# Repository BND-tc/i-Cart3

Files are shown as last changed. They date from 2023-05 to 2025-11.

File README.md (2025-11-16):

# i-Cart3

オープンソース移動ロボットプラットフォームi-Cart3 の制作に必要な情報のリポジトリ

## パーツリスト (Parts list)
60W/100W/200Wモーター版の組立に必要な部品構成表です

## 3Dモデルデータ (3D Model Data)
Parasolid形式とSTEP形式のモデルデータです

## 構成 (Configuraion)
システムおよび回路の構成の資料です

iCart3_Configuration.pdfを参考に配線をしてください

## ソフトウェア (Software)
i-Cart3用のソフトウェアおよび設定ファイルです

### yp-spur(BLVR対応)
> https://github.com/BND-tc/yp-spur

上記ビルドの際にはlibmodbusが必要となります

BLVRにはあらかじめ左右モータードライバにmxex設定ファイルを適用してください

### yp-spur単体実行例
> /usr/local/bin/ypspur-coordinator -d PORT_PATH --blvr -p PARAM_PATH

> /usr/local/bin/ypspur-coordinator -d /dev/ttyUSB0 --blvr -p /home/pi/iCart3_200W.param

### ros実行例
> rosrun ypspur_ros ypspur_ros _ypspur_bin:=/usr/local/bin/ypspur-coordinator _port:=[PORT_PATH]--blvr _param_file:=[PARAM_PATH] _compatible:=1

> rosrun ypspur_ros ypspur_ros _ypspur_bin:=/usr/local/bin/ypspur-coordinator _port:=/dev/ttyUSB0--blvr _param_file:=/home/pi/iCart3_200W.param _compatible:=1

<strong> --blvrオプションの記載をデバイスポートの直後にスペース無しで記載してください。</strong>

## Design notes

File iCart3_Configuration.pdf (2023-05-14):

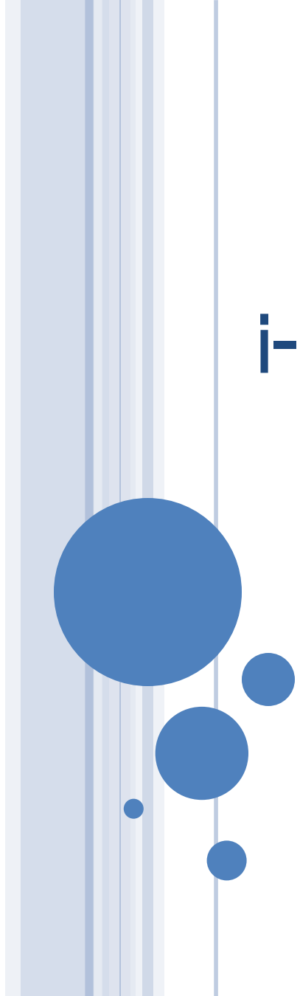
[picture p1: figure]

# i-Cart3

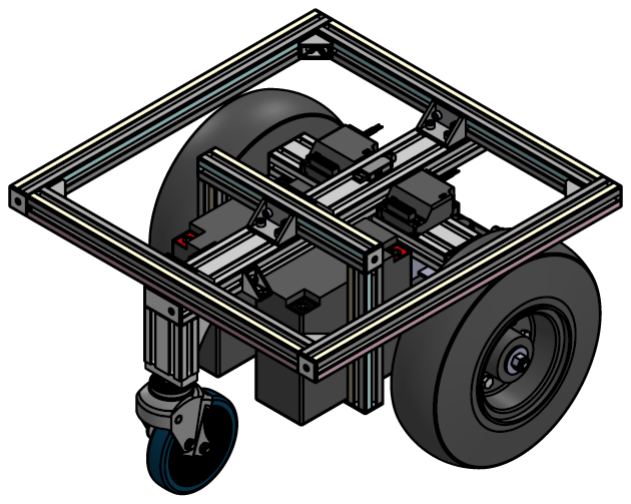
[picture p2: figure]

## https://github.com/BND-tc/i-Cart3

# 1 System Configuration

PC

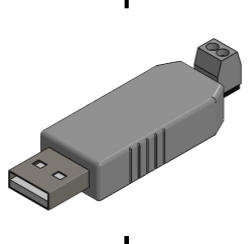
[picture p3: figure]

## USB-RS485 Convertor

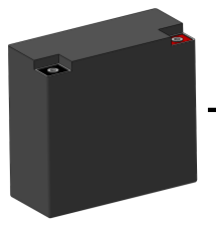
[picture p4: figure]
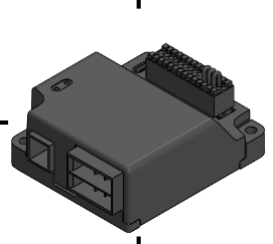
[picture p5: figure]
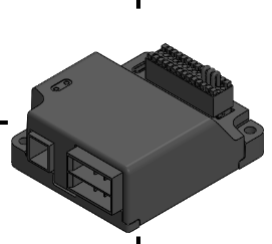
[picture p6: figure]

## BLVR

BLDC motor driver

## BLDC Motor

## Battery

# 2 Circuit Configuration

PC

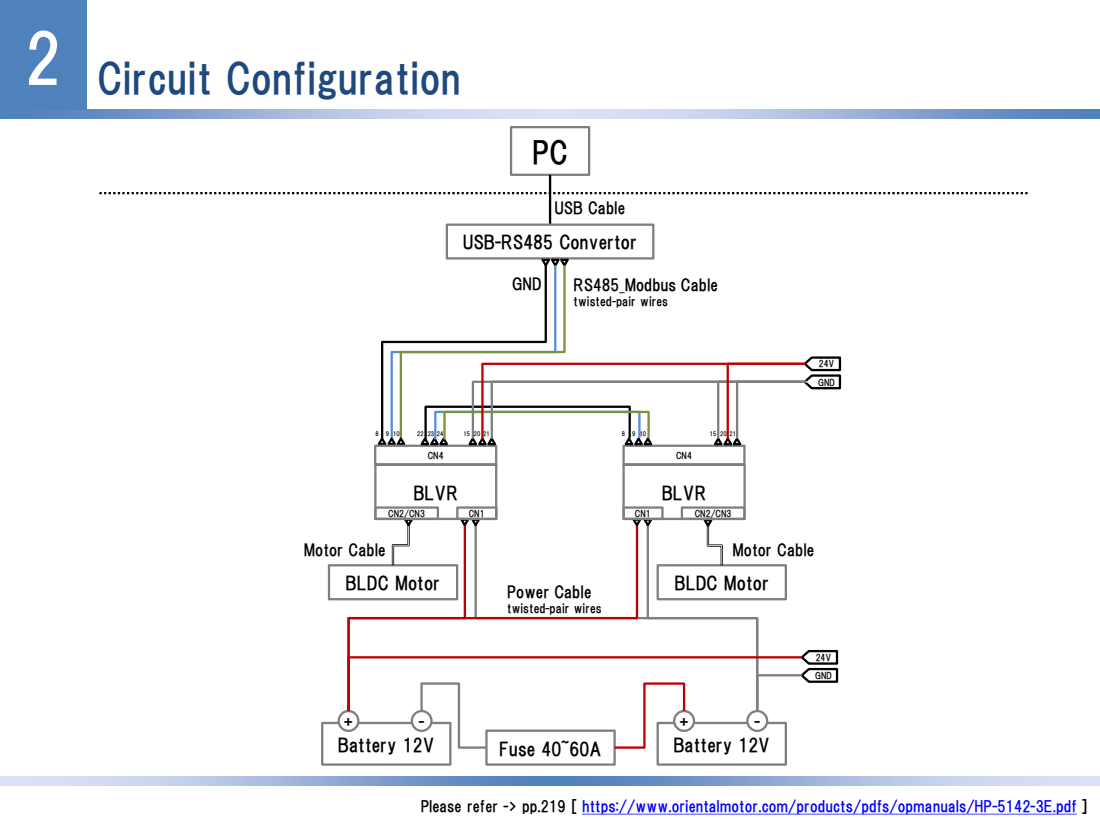
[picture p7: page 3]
USB-RS485 Convertor; BLVR; BLDC Motor; Fuse 40~60A; USB Cable; Motor; Cable; Motor Cable; Battery 12V; GND

RS485_Modbus Cable
twisted-pair wires

Power Cable

Please refer -> pp.219 [ https://www.orientalmotor.com/products/pdfs/opmanuals/HP-5142-3E.pdf ]

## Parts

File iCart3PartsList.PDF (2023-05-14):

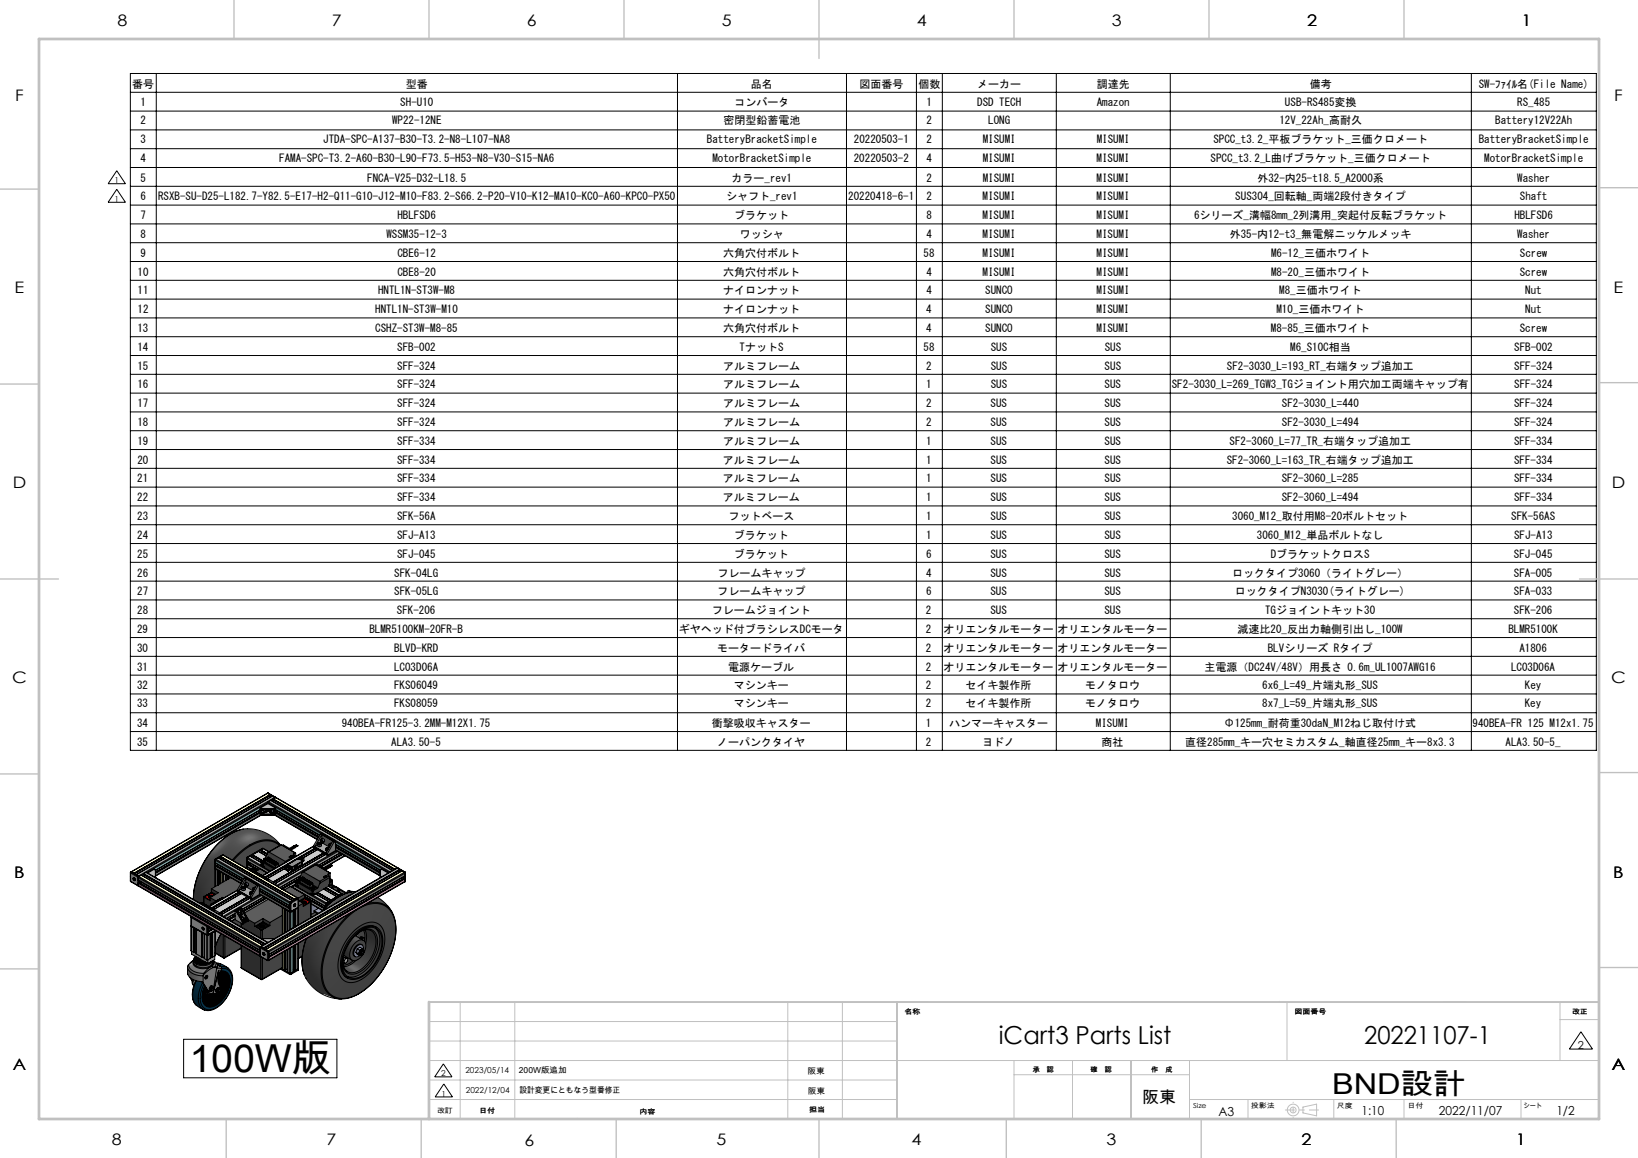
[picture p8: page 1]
2022/12/04 設計変更にともなう型番修正; 2023/05/14 200W版追加; iCart3 Parts List; BND設計; 1:10 投影法 改訂

番号 | 型番 | 品名 | 図面番号 | 個数 | メーカー | 調達先 | 備考 | SW-ﾌｧｲﾙ名(File Name)
1 | SH-U10 | コンバータ | | 1 | DSD TECH | Amazon | USB-RS485変換 | RS_485
2 | WP22-12NE | 密閉型鉛蓄電池 | | 2 | LONG | | 12V_22Ah_高耐久 | Battery12V22Ah
3 | JTDA-SPC-A137-B30-T3.2-N8-L107-NA8 | BatteryBracketSimple | 20220503-1 | 2 | MISUMI | MISUMI | SPCC_t3.2_平板ブラケット_三価クロメート | BatteryBracketSimple
4 | FAMA-SPC-T3.2-A60-B30-L90-F73.5-H53-N8-V30-S15-NA6 | MotorBracketSimple | 20220503-2 | 4 | MISUMI | MISUMI | SPCC_t3.2_L曲げブラケット_三価クロメート | MotorBracketSimple
5 | FNCA-V25-D32-L18.5 | カラー_rev1 | | 2 | MISUMI | MISUMI | 外32-内25-t18.5_A2000系 | Washer
6 | RSXB-SU-D25-L182.7-Y82.5-E17-H2-Q11-G10-J12-M10-F83.2-S66.2-P20-V10-K12-MA10-KC0-A60-KPC0-PX50 | シャフト_rev1 | 20220418-6-1 | 2 | MISUMI | MISUMI | SUS304_回転軸_両端2段付きタイプ | Shaft
7 | HBLFSD6 | ブラケット | | 8 | MISUMI | MISUMI | 6シリーズ_溝幅8mm_2列溝用_突起付反転ブラケット | HBLFSD6
8 | WSSM35-12-3 | ワッシャ | | 4 | MISUMI | MISUMI | 外35-内12-t3_無電解ニッケルメッキ | Washer
9 | CBE6-12 | 六角穴付ボルト | | 58 | MISUMI | MISUMI | M6-12_三価ホワイト | Screw
10 | CBE8-20 | 六角穴付ボルト | | 4 | MISUMI | MISUMI | M8-20_三価ホワイト | Screw
11 | HNTL1N-ST3W-M8 | ナイロンナット | | 4 | SUNCO | MISUMI | M8_三価ホワイト | Nut
12 | HNTL1N-ST3W-M10 | ナイロンナット | | 4 | SUNCO | MISUMI | M10_三価ホワイト | Nut
13 | CSHZ-ST3W-M8-85 | 六角穴付ボルト | | 4 | SUNCO | MISUMI | M8-85_三価ホワイト | Screw
14 | SFB-002 | TナットS | | 58 | SUS | SUS | M6_S10C相当 | SFB-002
15 | SFF-324 | アルミフレーム | | 2 | SUS | SUS | SF2-3030_L=193_RT_右端タップ追加工 | SFF-324
16 | SFF-324 | アルミフレーム | | 1 | SUS | SUS | SF2-3030_L=269_TGW3_TGジョイント用穴加工両端キャップ有 | SFF-324
17 | SFF-324 | アルミフレーム | | 2 | SUS | SUS | SF2-3030_L=440 | SFF-324
18 | SFF-324 | アルミフレーム | | 2 | SUS | SUS | SF2-3030_L=494 | SFF-324
19 | SFF-334 | アルミフレーム | | 1 | SUS | SUS | SF2-3060_L=77_TR_右端タップ追加工 | SFF-334
20 | SFF-334 | アルミフレーム | | 1 | SUS | SUS | SF2-3060_L=163_TR_右端タップ追加工 | SFF-334
21 | SFF-334 | アルミフレーム | | 1 | SUS | SUS | SF2-3060_L=285 | SFF-334
22 | SFF-334 | アルミフレーム | | 1 | SUS | SUS | SF2-3060_L=494 | SFF-334
23 | SFK-56A | フットベース | | 1 | SUS | SUS | 3060_M12_取付用M8-20ボルトセット | SFK-56AS
24 | SFJ-A13 | ブラケット | | 1 | SUS | SUS | 3060_M12_単品ボルトなし | SFJ-A13
25 | SFJ-045 | ブラケット | | 6 | SUS | SUS | DブラケットクロスS | SFJ-045
26 | SFK-04LG | フレームキャップ | | 4 | SUS | SUS | ロックタイプ3060（ライトグレー） | SFA-005
27 | SFK-05LG | フレームキャップ | | 6 | SUS | SUS | ロックタイプN3030(ライトグレー) | SFA-033
28 | SFK-206 | フレームジョイント | | 2 | SUS | SUS | TGジョイントキット30 | SFK-206
29 | BLMR5100KM-20FR-B | ギヤヘッド付ブラシレスDCモータ | | 2 | オリエンタルモーター | オリエンタルモーター | 減速比20_反出力軸側引出し_100W | BLMR5100K
30 | BLVD-KRD | モータードライバ | | 2 | オリエンタルモーター | オリエンタルモーター | BLVシリーズ Rタイプ | A1806
31 | LC03D06A | 電源ケーブル | | 2 | オリエンタルモーター | オリエンタルモーター | 主電源（DC24V/48V）用長さ 0.6m_UL1007AWG16 | LC03D06A
32 | FKS06049 | マシンキー | | 2 | セイキ製作所 | モノタロウ | 6x6_L=49_片端丸形_SUS | Key
33 | FKS08059 | マシンキー | | 2 | セイキ製作所 | モノタロウ | 8x7_L=59_片端丸形_SUS | Key
34 | 940BEA-FR125-3.2MM-M12X1.75 | 衝撃吸収キャスター | | 1 | ハンマーキャスター | MISUMI | Φ125mm_耐荷重30daN_M12ねじ取付け式 | 940BEA-FR 125 M12x1.75
35 | ALA3.50-5 | ノーパンクタイヤ | | 2 | ヨドノ | 商社 | 直径285mm_キー穴セミカスタム_軸直径25mm_キー8x3.3 | ALA3.50-5_

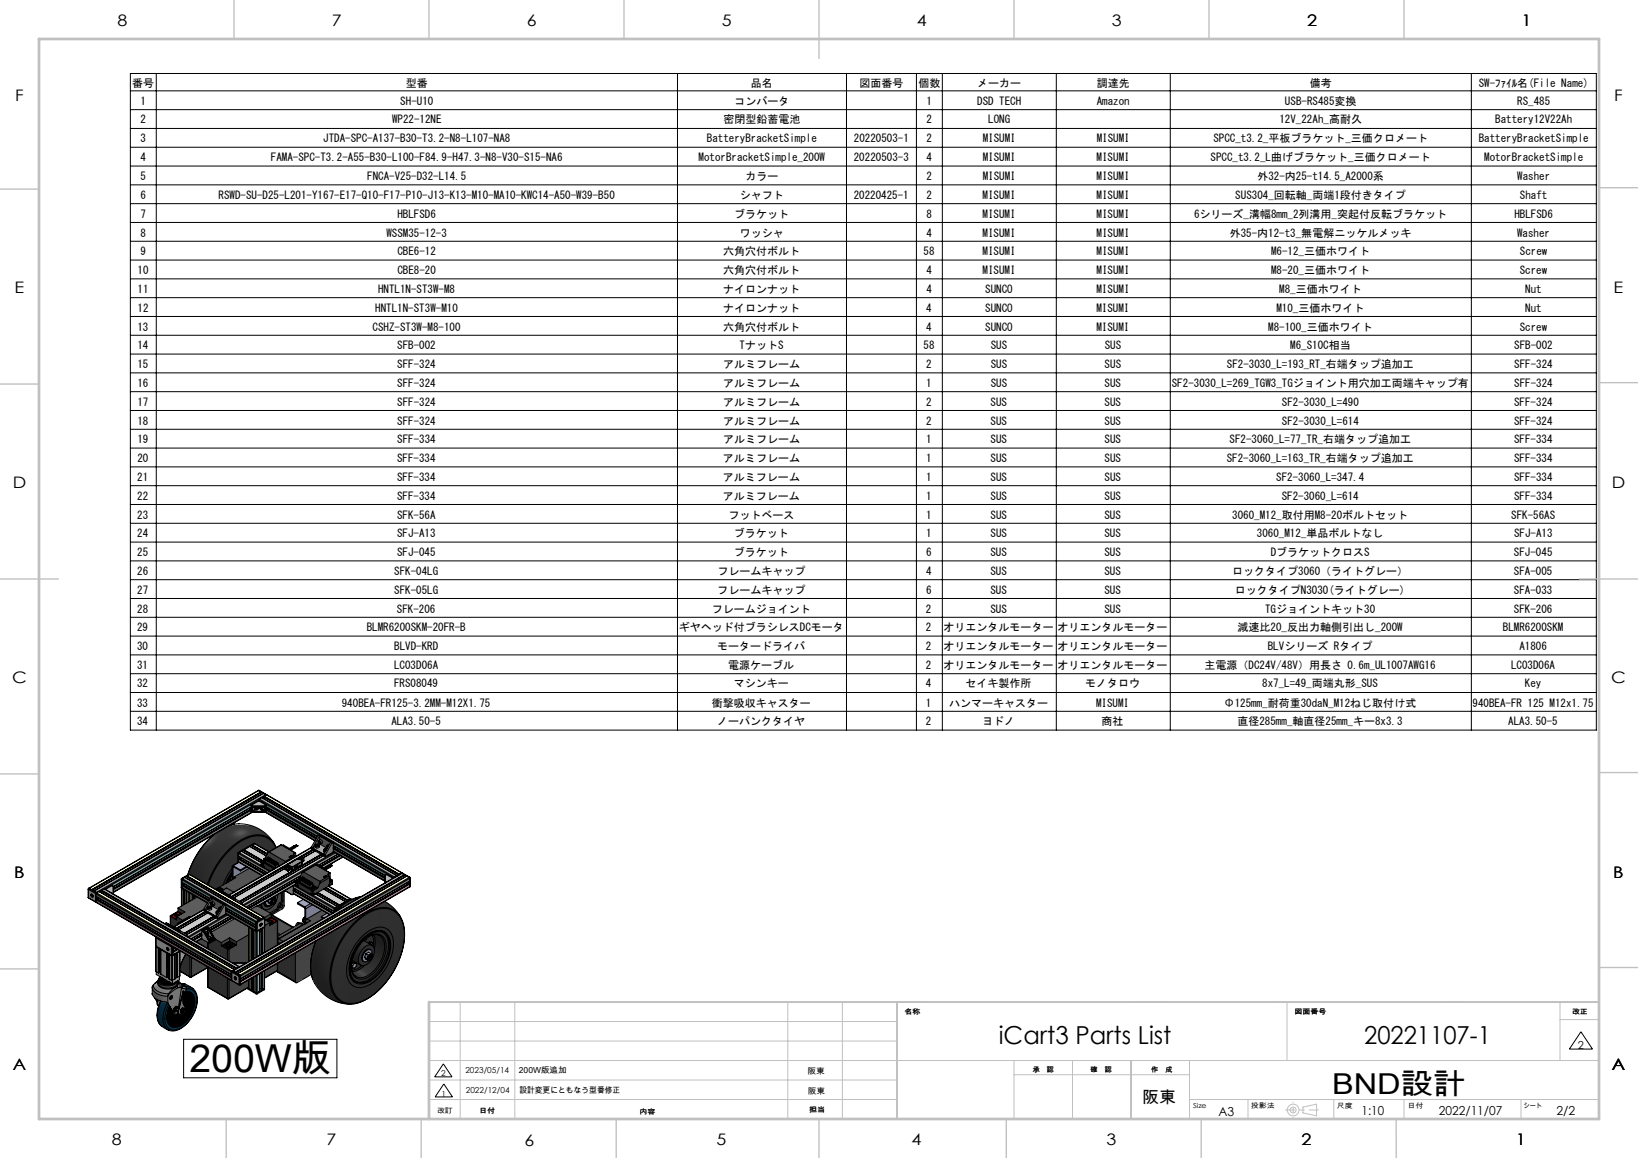
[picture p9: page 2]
2022/12/04 設計変更にともなう型番修正; 2023/05/14 200W版追加; iCart3 Parts List; BND設計; 1:10 投影法 改訂

番号 | 型番 | 品名 | 図面番号 | 個数 | メーカー | 調達先 | 備考 | SW-ﾌｧｲﾙ名(File Name)
1 | SH-U10 | コンバータ | | 1 | DSD TECH | Amazon | USB-RS485変換 | RS_485
2 | WP22-12NE | 密閉型鉛蓄電池 | | 2 | LONG | | 12V_22Ah_高耐久 | Battery12V22Ah
3 | JTDA-SPC-A137-B30-T3.2-N8-L107-NA8 | BatteryBracketSimple | 20220503-1 | 2 | MISUMI | MISUMI | SPCC_t3.2_平板ブラケット_三価クロメート | BatteryBracketSimple
4 | FAMA-SPC-T3.2-A55-B30-L100-F84.9-H47.3-N8-V30-S15-NA6 | MotorBracketSimple_200W | 20220503-3 | 4 | MISUMI | MISUMI | SPCC_t3.2_L曲げブラケット_三価クロメート | MotorBracketSimple
5 | FNCA-V25-D32-L14.5 | カラー | | 2 | MISUMI | MISUMI | 外32-内25-t14.5_A2000系 | Washer
6 | RSWD-SU-D25-L201-Y167-E17-Q10-F17-P10-J13-K13-M10-MA10-KWC14-A50-W39-B50 | シャフト | 20220425-1 | 2 | MISUMI | MISUMI | SUS304_回転軸_両端1段付きタイプ | Shaft
7 | HBLFSD6 | ブラケット | | 8 | MISUMI | MISUMI | 6シリーズ_溝幅8mm_2列溝用_突起付反転ブラケット | HBLFSD6
8 | WSSM35-12-3 | ワッシャ | | 4 | MISUMI | MISUMI | 外35-内12-t3_無電解ニッケルメッキ | Washer
9 | CBE6-12 | 六角穴付ボルト | | 58 | MISUMI | MISUMI | M6-12_三価ホワイト | Screw
10 | CBE8-20 | 六角穴付ボルト | | 4 | MISUMI | MISUMI | M8-20_三価ホワイト | Screw
11 | HNTL1N-ST3W-M8 | ナイロンナット | | 4 | SUNCO | MISUMI | M8_三価ホワイト | Nut
12 | HNTL1N-ST3W-M10 | ナイロンナット | | 4 | SUNCO | MISUMI | M10_三価ホワイト | Nut
13 | CSHZ-ST3W-M8-100 | 六角穴付ボルト | | 4 | SUNCO | MISUMI | M8-100_三価ホワイト | Screw
14 | SFB-002 | TナットS | | 58 | SUS | SUS | M6_S10C相当 | SFB-002
15 | SFF-324 | アルミフレーム | | 2 | SUS | SUS | SF2-3030_L=193_RT_右端タップ追加工 | SFF-324
16 | SFF-324 | アルミフレーム | | 1 | SUS | SUS | SF2-3030_L=269_TGW3_TGジョイント用穴加工両端キャップ有 | SFF-324
17 | SFF-324 | アルミフレーム | | 2 | SUS | SUS | SF2-3030_L=490 | SFF-324
18 | SFF-324 | アルミフレーム | | 2 | SUS | SUS | SF2-3030_L=614 | SFF-324
19 | SFF-334 | アルミフレーム | | 1 | SUS | SUS | SF2-3060_L=77_TR_右端タップ追加工 | SFF-334
20 | SFF-334 | アルミフレーム | | 1 | SUS | SUS | SF2-3060_L=163_TR_右端タップ追加工 | SFF-334
21 | SFF-334 | アルミフレーム | | 1 | SUS | SUS | SF2-3060_L=347.4 | SFF-334
22 | SFF-334 | アルミフレーム | | 1 | SUS | SUS | SF2-3060_L=614 | SFF-334
23 | SFK-56A | フットベース | | 1 | SUS | SUS | 3060_M12_取付用M8-20ボルトセット | SFK-56AS
24 | SFJ-A13 | ブラケット | | 1 | SUS | SUS | 3060_M12_単品ボルトなし | SFJ-A13
25 | SFJ-045 | ブラケット | | 6 | SUS | SUS | DブラケットクロスS | SFJ-045
26 27 | SFK-04LG SFK-05LG | フレームキャップ | | 4 6 | SUS | SUS | ロックタイプ3060（ライトグレー） ロックタイプN3030(ライトグレー) | SFA-005 SFA-033

28 | SFK-206 | フレームジョイント | | 2 | SUS | SUS | TGジョイントキット30 | SFK-206
29 | BLMR6200SKM-20FR-B | ギヤヘッド付ブラシレスDCモータ | | 2 | オリエンタルモーター | オリエンタルモーター | 減速比20_反出力軸側引出し_200W | BLMR6200SKM
30 | BLVD-KRD | モータードライバ | | 2 | オリエンタルモーター | オリエンタルモーター | BLVシリーズ Rタイプ | A1806
31 | LC03D06A | 電源ケーブル | | 2 | オリエンタルモーター | オリエンタルモーター | 主電源（DC24V/48V）用長さ 0.6m_UL1007AWG16 | LC03D06A
32 | FRS08049 | マシンキー | | 4 | セイキ製作所 | モノタロウ | 8x7_L=49_両端丸形_SUS | Key
33 | 940BEA-FR125-3.2MM-M12X1.75 | 衝撃吸収キャスター | | 1 | ハンマーキャスター | MISUMI | Φ125mm_耐荷重30daN_M12ねじ取付け式 | 940BEA-FR 125 M12x1.75
34 | ALA3.50-5 | ノーパンクタイヤ | | 2 | ヨドノ | 商社 | 直径285mm_軸直径25mm_キー8x3.3 | ALA3.50-5

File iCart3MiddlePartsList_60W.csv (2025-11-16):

番号 | 型番 | 品名 | 図面番号 | 個数 | メーカー | 備考
1 | B0BFPCMY7J | タイヤ |  | 2 | Amazon | 12インチ車椅子用パックレスタイヤ https://amzn.asia/d/eucIvon
2 | SH-U10 | コンバータ |  | 1 | DSD TECH | USB-RS485変換
3 | WP12-12 | 完全密封型鉛蓄電池 |  | 2 | LONG | 12V12Ah_F2端子
4 | JTABS-AM-A97-B65-T3-X10-G40-N5-L27-V65-W55-MA4 | BLVR固定板 |  | 2 | MISUMI | A5052t3_取付板・ブラケット－フリー寸法タイプ－ JTAAS
5 | HFS5-2020-130-TPW | アルミフレーム |  | 4 | MISUMI | エコノミータイプ_L=130_両端タップ
6 | HFS5-2020-205-TPW | アルミフレーム |  | 6 | MISUMI | エコノミータイプ_L=205_両端タップ
7 | NFS5-2020-350-LCP-RCP-AH145 | アルミフレーム |  | 2 | MISUMI | エコノミータイプ_L=350_レンチ穴複数
8 | NFS5-2020-455-LCV-RCP-AH250-AV30-AP115 | アルミフレーム |  | 2 | MISUMI | エコノミータイプ_L=455_レンチ穴複数
9 | NFS5-2040-60-TPW | アルミフレーム2040 |  | 2 | MISUMI | エコノミータイプ_L=60_両端タップ
10 | NFS5-2040-245-LCH-RCH | アルミフレーム2040 |  | 1 | MISUMI | エコノミータイプ_L=245_左右端水平レンチ穴
11 | HNTT5-5 | アルミフレーム用先入れナット |  | 22 | MISUMI | 5シリーズ用_M5_三価クロメート
12 | C-CJFJ100-T | キャスター |  | 2 | MISUMI | 車輪径100mm_キャスタ TPRキャスタ 自在タイプ
13 | NBQE-ABS-A92-B64-T8-F72-G44.5-M8-L36-V20-W20-Q2.5-ZA5-CAC4-CBC4-CCC4-CDC4 | キャスター固定板 |  | 2 | MISUMI | ABSt8_樹脂ﾌﾟﾚｰﾄ･ﾌﾞﾛｯｸ-ｴﾝﾌﾟﾗ系-
14 | RSXB-SU-D15-L144-Y74-E55-H41-Q12-G8-J10-M8-F15-S2-P9-V8-K10-MA8-KC3-A60 | シャフト |  | 2 | MISUMI | 回転軸-両端1段付きﾀｲﾌﾟ/両端2段付きﾀｲﾌﾟｰ
15 | SHRE-AM-H56-L21-D28-T10-P15-Q44-M5-F0-MA0-MXC | ダイヤ固定用ハブ |  | 2 | MISUMI | ｼｬﾌﾄ/支柱ﾎﾙﾀﾞ-ｽﾄﾚｰﾄﾀｲﾌﾟ-
16 | HNTL1N-ST3W-M6 | ナイロンナット |  | 8 | MISUMI | M6_三価クロメート
17 | HNTL1N-ST3W-M8 | ナイロンナット |  | 4 | MISUMI | M8_三価ホワイト
18 | HCJ5 | ブラインドジョイント |  | 28 | MISUMI | 5シリーズ_スクリュージョイント
19 | HPTSD5 | プレートブラケット |  | 1 | MISUMI | 5シリーズ用正方形t2.3_三価クロメート
20 | JTAAS-AM-A57-B79-T3-X6-G66.5-N6-L41.8-W63-NA5 | モータ固定板 |  | 4 | MISUMI | A5052t3_板金 取付板・ブラケット－フリー寸法タイプ－ JTAAS
21 | SPWF8 | ワッシャ |  | 4 | MISUMI | 外17-内8.4-t1.6_SUS
22 | KESS5-60 | 平行キー |  | 2 | MISUMI | W=5_L=60_両R_ステンレス
23 | CBE4-15 | 六角穴付ボルト |  | 4 | MISUMI | M4-15_三価ホワイト
24 | CBE5-8 | 六角穴付ボルト |  | 22 | MISUMI | M5-8_三価ホワイト
25 | CBE5-20 | 六角穴付ボルト |  | 6 | MISUMI | M5-20_三価ホワイト
26 | CBE6-70 | 六角穴付ボルト |  | 8 | MISUMI | M6-70_三価ホワイト
27 | CBE8-10 | 六角穴付ボルト |  | 8 | MISUMI | M8-10_三価ホワイト
28 | BLMR460SHK-GFV/GFS4G30FR | ギアヘッド付ブラシレスモータ |  | 2 | オリエンタルモーター | BLVシリーズRタイプ_中空軸フラットギヤヘッド_60W
29 | BLVD-KRD | モータードライバ |  | 2 | オリエンタルモーター | BLVシリーズ Rタイプ
30 | LC03D06A | 電源ケーブル |  | 2 | オリエンタルモーター | 主電源（DC24V/48V）用長さ 0.6m_UL1007AWG16

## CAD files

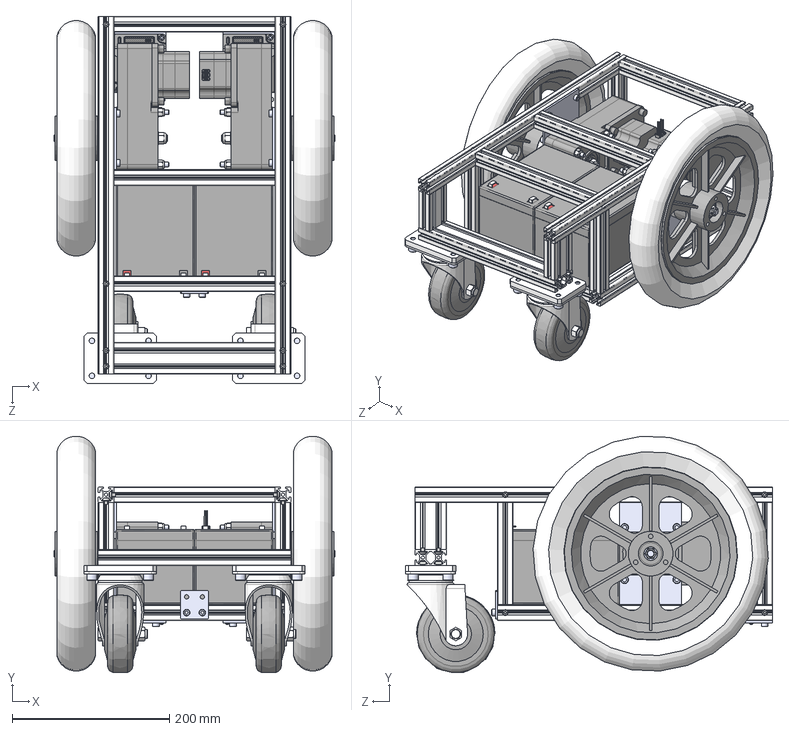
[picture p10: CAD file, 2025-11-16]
iCart3Middle_60W.STEP
357.0 x 300.9 x 467.0 mm
A1870 x 2
12inchWheel_rev1 x 2
Battery x 2
A1806 x 2
12inchWheelHub_rev1 x 2
Screw_六角穴付ボルト_M5-20 x 6
Shaft60W_rev1 x 2
Nut_ナイロンナット_M8 x 4
Washer_17-8.4-t1.6 x 4
MotorMountPlate x 4
CasterMountPlate x 2
C-CJFJ100-T_b.stp x 2
C-CJFJ100-T_p.stp x 2
C-CJFJ100-T_w.stp x 2
NFS5-2020_L1 x 2
NFS5-2020_L3 x 4
NFS5-2020_L2 x 6
NFS5-2020_L4 x 2
NFS5-2040_L1
NFS5-2040_L2 x 2
HCJ_Joint_Plate5_p x 28
HCJ_Screw5_s x 28
Screw_六角穴付ボルト_M6-70 x 8
Nut_ナイロンナット_M6 x 8
Key_5RR60 x 2
Screw_六角穴付ボルト_M8-10 x 8
CircuitMountPlate x 2
Screw_六角穴付ボルト_M4-15 x 4
HNTT5-5 x 22
Screw_六角穴付ボルト_M5-8 x 22
HPTSD5
F32FSS-03V-KX x 2
Wire_UL1007_AWG16_Red x 2
Wire_UL1007_AWG16-Black x 2
RS_485

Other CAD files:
iCart3Middle_60W.x_b
iCart3_100W.x_b

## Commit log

2022-11-07 Added the parts list and the 3d model data of i-Cart3 100W version.
    [iCart3PartsList.csv, iCart3_100W.x_b]
2022-12-04 Updated parts list.
    [iCart3PartsList.csv]
2023-05-14 Update the parts list and the 3d model data of i-Cart3 200W version
    [iCart3PartsList.csv, iCart3PartsList_100W.csv, iCart3PartsList_200W.csv]
2023-06-18 Update README.md, Added parameter files
    [iCart3_200W.param]
2023-11-16 Update README.md, Bugfix mxex files -> improve max wheel speed and torque
2025-11-16 Added i-Cart3Middle_60W
    [iCart3MiddlePartsList_60W.csv, iCart3Middle_60W.STEP, iCart3Middle_60W.x_b]
